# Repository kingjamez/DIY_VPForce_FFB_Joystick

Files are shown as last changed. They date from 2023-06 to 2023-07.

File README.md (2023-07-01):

Work in Progress
This project contains CAD files necessary for the mechanical assembly of a base of the VPForce kit (2x57BLF03 + USB kit).
Why Fork from Mabo1972? Mabo's design is great, has a few small errors but generally "just works". If that design works for you I can do nothing but recommend it.
No files from Mabo1972's design are present here. Everything has been rebuilt from the ground up in CAD. Almost everything should be Mabo compatible such that if you decide something in that design is better, it should all work together (within reason, obviously all the laser cut walls need to work together, but the spacing of the motors / gears is compatible) . Most of my changes accomodate the tools I have or the materials I can get in the USA. I also plan to put together a kit of all of the below and offer it for sale.

One major change is that this design uses plywood available in the U.S. 1/4" rather than the 8mm from the original files. My laser cutter can only do 1/4" plywood reliably and with low Kerf so I double stack each cut for a total of 1/2" thick walls. In some cases like the top, the bottom peice is different from the top piece in order to accomodate 2.5D features like switchs, pots, and panel mount connectors.

An additional change is the power input of XT60. I like this connector for it's high reliability. You'll likely need to solder a connector on to whatever power supply you buy as it is rare to find power supplies with XT60 from the factory. 

Additionally this adds different gear profiles that allow an option for higher gear ratios and eliminates the need to buy exact belt sizes or worry about belt tensioning via motor slots or idlers. 
It also includes a gimbal adapter allowing 0.75" square aluminum tubing as an extension before the actual stick is installed using standard Thrustmaster / Virpil threads (M35x2). 

To that end, some amount of "handiness" is required for this kit. It is not for folks who do not enjoy DIY. There will be crimping, soldering, and troubleshooting required. If you do buy a kit realize that I'm not doing this for profit, I'm publishing this so that more people can get into force feedback because it is awesome and VPForce is fantastic. If the wait list was not as long as it is (as of July 2023) then I would not publish this. For the price of the "real" Rhino, it's very much worth it to just buy it from VPForce if you can handle the wait list.

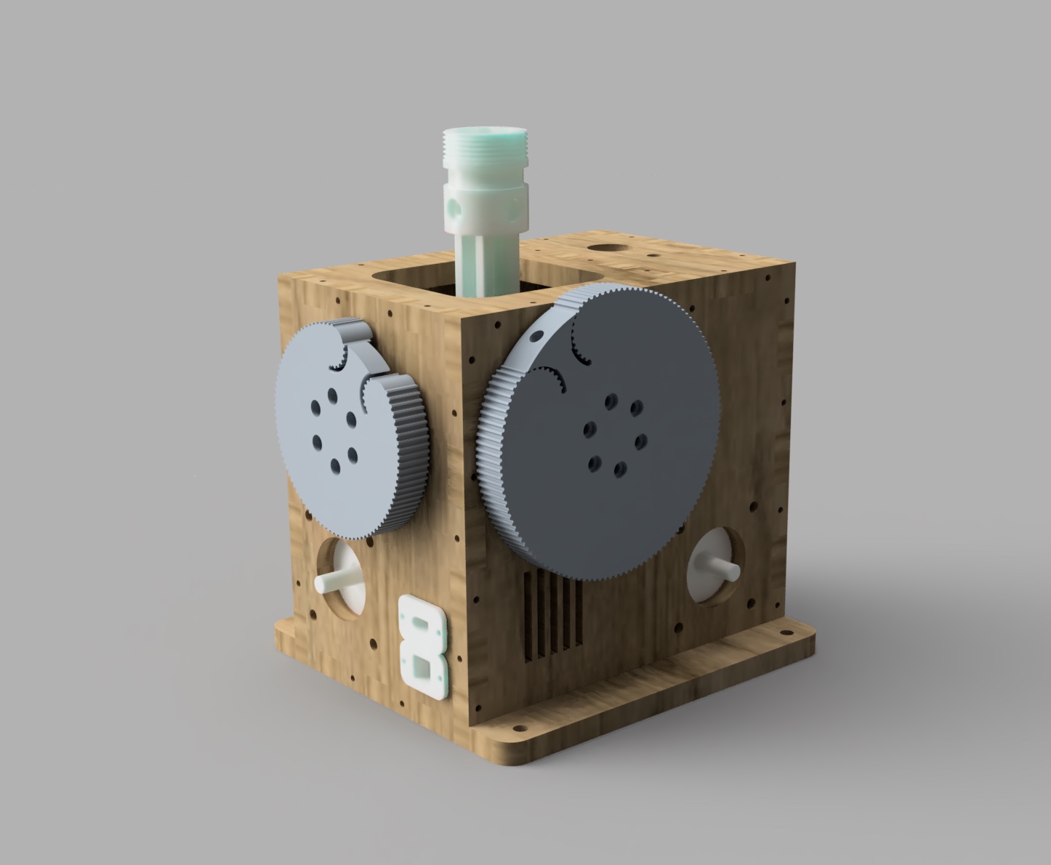
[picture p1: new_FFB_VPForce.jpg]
 

3d-print-parts - all elements which need to be printed  
DXF - drawings for case parts for laser cutting  
CAD - F3D and STEP

Note that none of the below links are affiliate links. I make nothing from these links.

## Bill of Materials

| VPForce Kit | Quantity | Link |
|--- |:---:|-----:|
|57BLF03 - 57x101mm - 1.6Nm peak - 1.24kg - NEMA23|1|[VPForce Kit Order Sheet](http://order.vpforce.eu) |

| Print Parts | Quantity |
| --- |:---:|
|bearing_retainer_half|4|
|bearing_retainer|4|
|GIMBAL_ARM_BEARING_PILLOW|4|
|GIMBAL_ARM_FRAME|2|
|GIMBAL_CORE_JOINT_6mm|1|
|GIMBAL_STICK_CONNECTOR |1|
|Top_Adapter |1|
|PULLEY_96T|1|
|PULLEY_128T|1|
|VPForce_Controller_Holder|1|
|USB-B Panel Mount |1|

| LaserCut Parts Plywood 1/4"| Quantity |
| --- |:---:|
|Rear|2|
|Bottom|2|
|Front Front|1|
|Front Rear| 1|
|Left Side|2|
|Mid Support|2|
|Right Side|2|
|Top Top |1|
|Top Bottom |1|

| Bearings | Quantity  | Link |
| --- | --- | ---- |
| 6802 (24x15x5mm) | 8  | [JSB](https://jsbgreatbearings.com/68022rs-c-9_87/68022rs-premium-6802-2rs-seal-bearing-6802-ball-bearings-6802-rs-abec3-p-310.html)|
| 6808 (52x40x7mm) | 4  | [JSB](https://jsbgreatbearings.com/68082rs-c-9_300/68082rs-two-side-rubber-seals-bearing-6808rs-ball-bearings-6808-rs-p-676.html)|
| F625 (16x5x5mm, 18x1mm flange)| 2  | [JSB](https://jsbgreatbearings.com/f625zz-c-3_505/flange-ball-bearing-f625zz-metal-shields-f625zz-high-quality-f625-zz-p-1022.html) |

Alternate source for bearings: [123bearings](https://123bearings.com)
Ebay is also a good source for these standard size bearings.

| Motor pulley | Quantity  | Link |
| --- | --- | ---- |
| 3GT -16Tooth-8mm Bore | 2  |[ebay](https://www.ebay.com/itm/225592008473) |

| Belts 		| Quantity  | Link |
| --- | --- | ---- |
| 3GT-3mm Open Loop Timing Belt | 1 meter|[ebay](https://www.ebay.com/itm/224467077690?var=523250397611) |

|Electronics |Quantity | Link|
|---| --- | ---- |
|DIN5 Female Connector | 1  |[Digikey](https://www.digikey.com/en/products/detail/cui-devices/MD-50PL100/500828)|
|XT 60 Panel Mount Male & Female  | 2 (1ea)  |[Amazon](https://a.co/d/0gA4TEY) |
|19V 180W+ DC Power Supply | 1  | [Amazon](https://a.co/d/iy1mMZF)|
|Emergency Cutoff Switch 10A| 1  |[Amazon](https://a.co/d/2vKUG6i) |
|10k Potentiometer | 2  |[Amazon](https://a.co/d/dEJRBl2) |
|10 Conductor Wire (1ft req) | 1 |[Amazon](https://a.co/d/eSipjIW) |
|80mm 24V fan | 1| [Amazon](https://a.co/d/5TQbYCp)|
|USB-B Panel Mount | 1| [Amazon](https://a.co/d/8rjkGPT)|
|Alternate USB-C Panel Mount with adapter| 1 ea| [USB-C Panel Mount](https://a.co/d/2RB9gru) [USB-C wire plug](https://a.co/d/2es5Zsm)|
|DIN5 Male if you want to make an extension |1| [Digikey](https://www.digikey.com/en/products/detail/cui-devices/MD-50/96914)|

|Hardware |Quantity | Link|
|---| --- | ---- |
|M4x12mm Bolts for Bearing Pillows  |  8  | [Bolt Depot](https://www.boltdepot.com/Product-Details.aspx?product=13341) |
|M6x20mm Motor Mount Bolts |  8  | [Bolt Depot](https://www.boltdepot.com/Product-Details.aspx?product=6540) |
|M6 Motor Mount Lock Washers |  8  | [Bolt Depot](https://www.boltdepot.com/Product-Details.aspx?product=4813) |
|M6 Motor Mount Washers |  8  | [Bolt Depot](https://www.boltdepot.com/Product-Details.aspx?product=4516) | 
|M5x12mm Aluminum Square Tube to gimbal  | 8 | [Bolt Depot](https://www.boltdepot.com/Product-Details.aspx?product=13344) |
|M5 Flange nut for center gimbal | 2| [Bolt Depot](https://www.boltdepot.com/Product-Details.aspx?product=17684)|
|M5x50mm Bolt through center gimbal connector | 1| [Bolt Depot](https://www.boltdepot.com/Product-Details.aspx?product=13344) |
|M5 Washer |  2 | [Bolt Depot](https://www.boltdepot.com/Product-Details.aspx?product=4515)|
|M5 Lock Nut | 1 | [Bolt Depot](https://www.boltdepot.com/Product-Details.aspx?product=4794)|
|M4 Locking Hex Nuts for Gimbal Arms | 12| [Bolt Depot](https://www.boltdepot.com/Product-Details.aspx?product=4793)|
|M4x35mm Cap Bolts to connect gears to Gimbal Arms | 12 | [Bolt Depot](https://www.boltdepot.com/Product-Details.aspx?product=18949)|
|M2.5 screws to hold VPForce board to standoffs |4|[Bolt Depot](https://www.boltdepot.com/Product-Details.aspx?product=24854) |
|M3x25 bolts to hold bearing holders in place | 16|[Bolt Depot](https://www.boltdepot.com/Product-Details.aspx?product=18942) |
|M3 lock nuts | 16|[Bolt Depot](https://www.boltdepot.com/Product-Details.aspx?product=4792)|
|M3 lock washers | 16 | [Bolt Depot](https://www.boltdepot.com/Product-Details.aspx?product=4810)|
|M3 washers |32 |[Bolt Depot](https://www.boltdepot.com/Product-Details.aspx?product=4513)|
|Bolt Depot cart with all the above plus 1 extra ||[Bolt Depot](https://www.boltdepot.com/cart/215497)|
|M3 screws to install VPForce board into chassis |2| Find in parts bin |
|#8-1" Self Drilling Wood Screws |  1pkg | [Amazon](https://a.co/d/aeVexTG)|
|Hardware to mount to your SIM PIT | 4 | 5mm mounting holes|
|M4 Inserts High Quality | 8| [Amazon](https://a.co/d/0r7RgK8)|

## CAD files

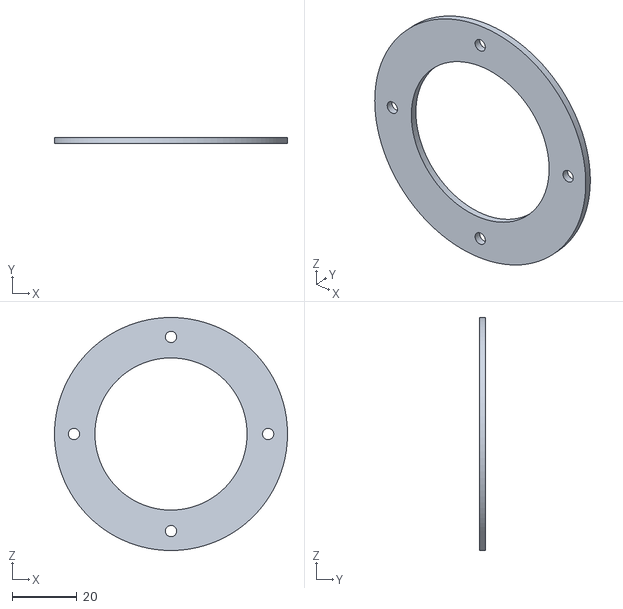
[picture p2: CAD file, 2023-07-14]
3d-print-parts/Bearing Retainer.stl
72.0 x 2.00 x 72.0

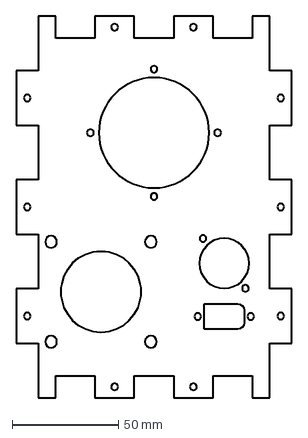
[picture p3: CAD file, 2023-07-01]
DXF/Front_Front.dxf
130.0 x 180.0 mm

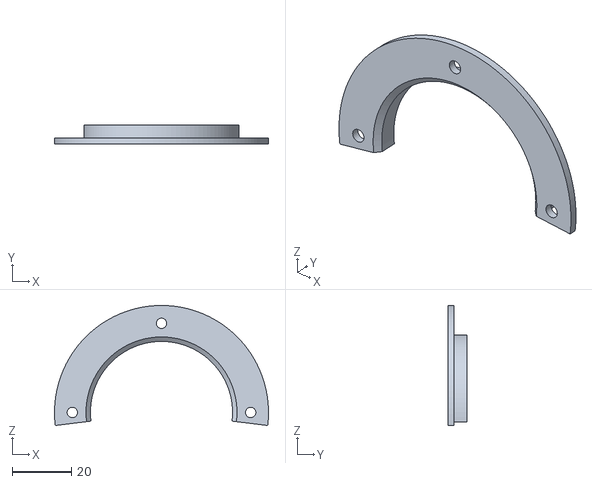
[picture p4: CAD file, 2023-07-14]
3d-print-parts/Bearing Retainer Half.stl
72.0 x 6.30 x 40.4

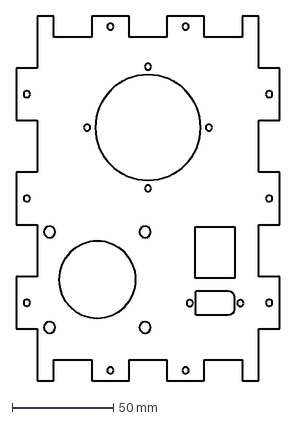
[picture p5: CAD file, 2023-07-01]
DXF/Front_Rear.dxf
130.0 x 180.0 mm

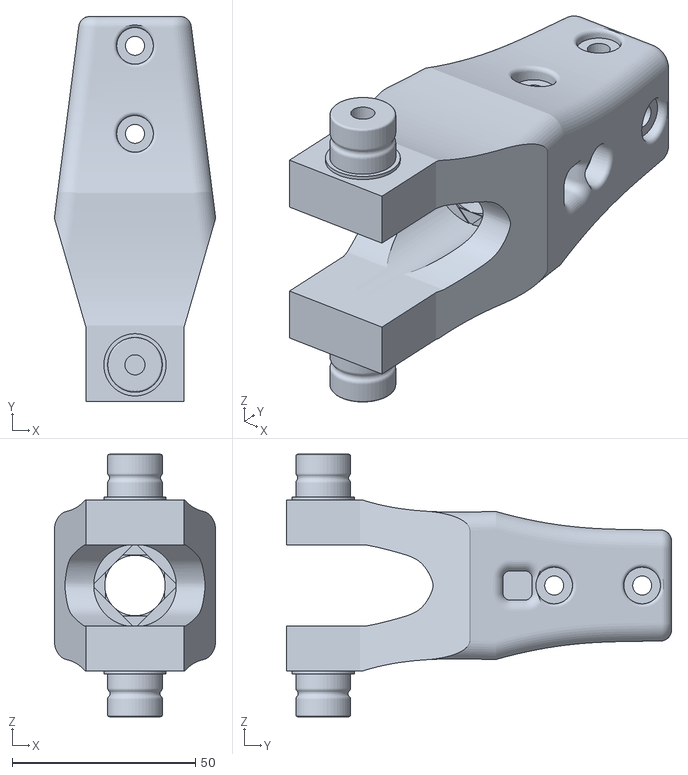
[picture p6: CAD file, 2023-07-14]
3d-print-parts/Gimbal_Stick_Connector_Square_Tube_Min_support.stl
44.0 x 105.0 x 71.6

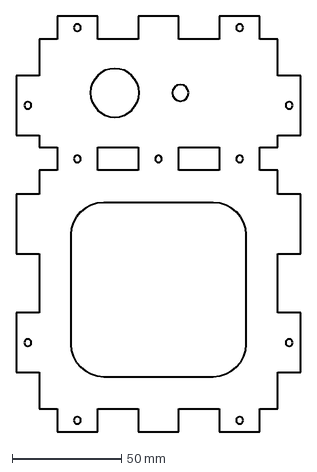
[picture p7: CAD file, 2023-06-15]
DXF/FFB_Top_Top.dxf
130.0 x 190.0 mm

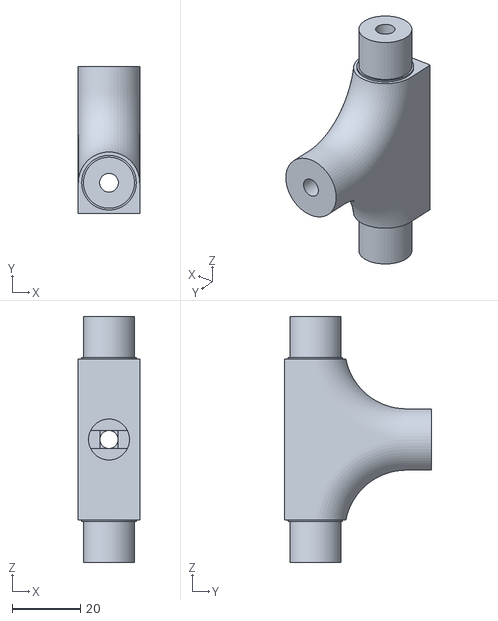
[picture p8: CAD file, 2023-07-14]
3d-print-parts/Gimbal_Core_Square_min_support.stl
18.0 x 43.0 x 72.0

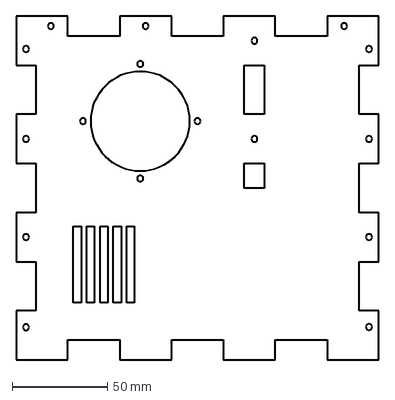
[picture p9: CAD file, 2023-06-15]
DXF/FFB_Left_Side.dxf
190.0 x 180.0 mm

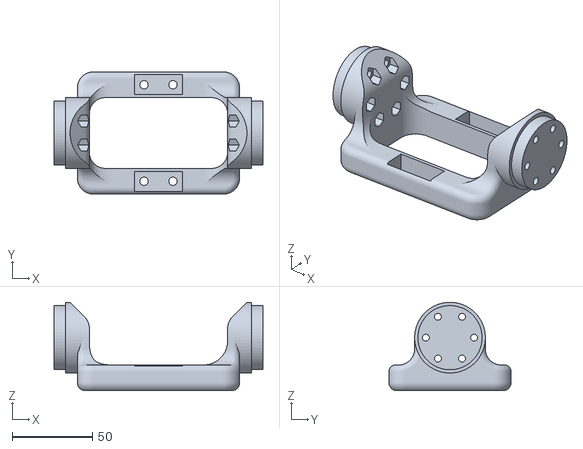
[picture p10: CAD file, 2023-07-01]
3d-print-parts/New_Gimbal_Arm v9.stl
130.0 x 76.0 x 55.0

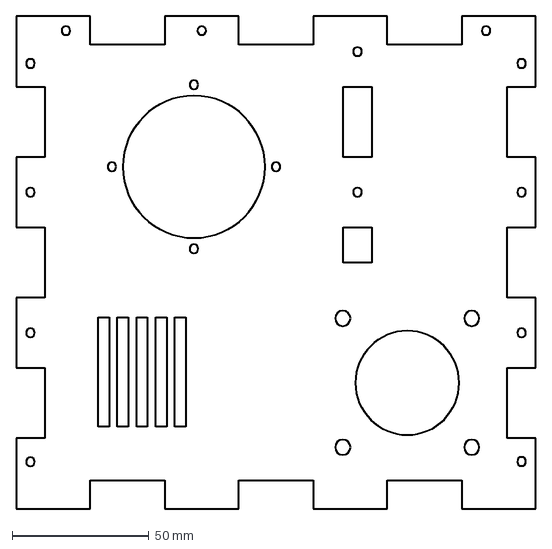
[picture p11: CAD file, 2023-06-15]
DXF/FFB_Right_Side.dxf
190.0 x 180.0 mm

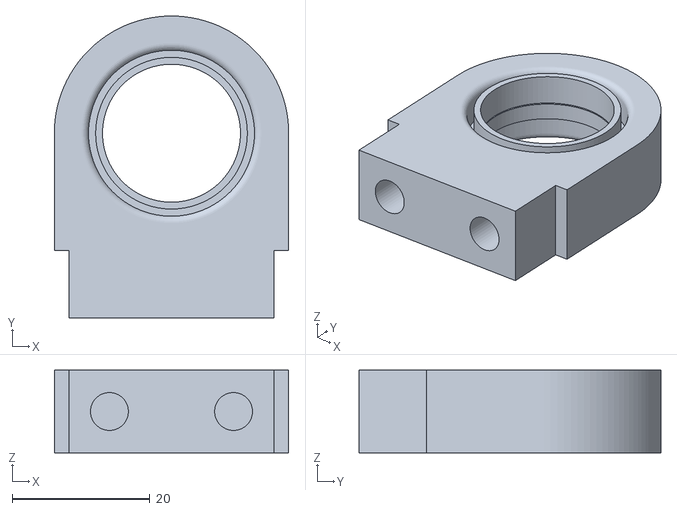
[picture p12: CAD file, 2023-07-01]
3d-print-parts/SQ_Pillow_Block_supports v4.stl
34.0 x 43.8 x 12.0

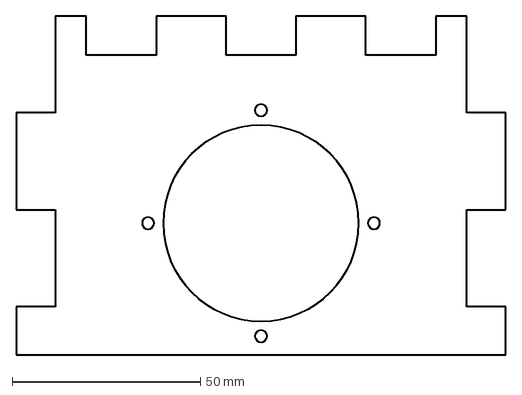
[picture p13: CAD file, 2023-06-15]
DXF/FFB_Mid_Panel.dxf
130.0 x 90.0 mm

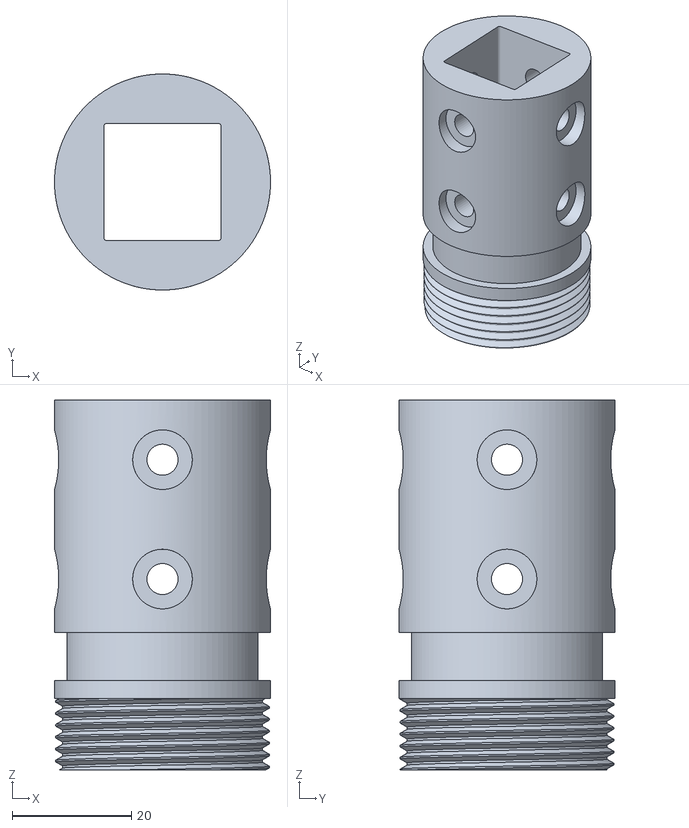
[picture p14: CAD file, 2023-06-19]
3d-print-parts/Top_Adapter_FFB v11.stl
36.2 x 36.2 x 62.0

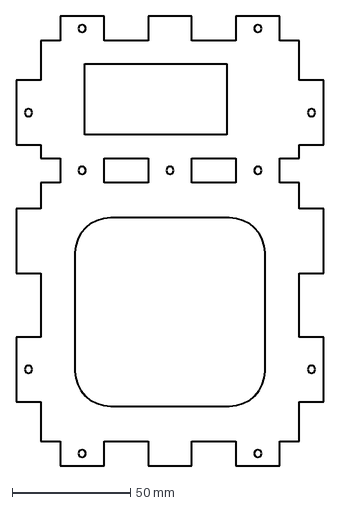
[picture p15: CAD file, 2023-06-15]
DXF/FFB_Top_2ndlayer.dxf
130.0 x 190.0 mm

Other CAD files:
3d-print-parts/VPForce_Board_Holder v1.stl
DXF/FFB_Rear.dxf
DXF/FFB_Bottom.dxf

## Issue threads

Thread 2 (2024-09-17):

3

peterb154, 2024-09-17:
Hey @kingjamez I just finished cutting and assembling your laser cut parts. Very nice. Ive started the 3d printing and sure do appreciate the improvements you've made for printability.

The 96 and 128T pulley's are missing from the 3d-printed-parts https://github.com/kingjamez/DIY_VPForce_FFB_Joystick/tree/master/3d-print-parts
Any chance you could throw those into the project?

So is the USB-B panel mount, but that is less of an issue for me.
